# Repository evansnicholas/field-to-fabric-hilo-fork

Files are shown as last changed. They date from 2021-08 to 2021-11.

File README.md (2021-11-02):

# Who is Studio HILO?

Studio HILO is a Berlin-based studio for textile innovation. We rethink the textile industry by offering open tools, trainings and consultancy for small-scale textile manufacturing environments. HILO’s mission is to create playgrounds for independent yarn production. The HILO Spinning Machine (and Software) is an open source project by Studio HILO and allows users to produce their own customized yarn. More information: www.studiohilo.com

# What can you do with the HILO Spinning Machine/Software?

With hardware (HILO Spinning Machine) and software (HILO App) you can create different kinds of yarns. The software helps you to design and plan the yarn digitally – for weaving or knitting textiles. The hardware allows you to spin and twist the personalized yarn, all you have to do is to insert raw fibres of your choice (e.g. wool, silk, plastics) and press play. This is a tool for prototyping and experimenting!

# How does this instruction work?

We made a step by step instruction for materials order, hardware construction and software control. Just follow the order of the folders and in each folder you will find a readme.pdf that instructs you – please read it first of all.

# What are the steps?
* Introduction
* List of Parts
* Files
* Software
* Hardware
* How to start spinning

# What is the status quo of this project?

We documented every part for the HILO Spinning Machine 3.0 / Software but we continue working on both. This project is at an early stage of development, every piece of hardware and software is in beta version.

# How to reach out for support?

We built this, but we need your help to adjust and improve the current prototype. Send us your ideas, experiments, bugs and improvements. We are happy to see our project grow! Get in touch with us via diy@studiohilo.com. Have fun!

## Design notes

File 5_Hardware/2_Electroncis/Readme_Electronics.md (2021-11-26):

# Electronics 

In this scene you will connect all necessary components to make the HILO Spinning Machine work. In the electronic schematic and machine diagram you can see where and how the components are connected.

## Electronic Schematic

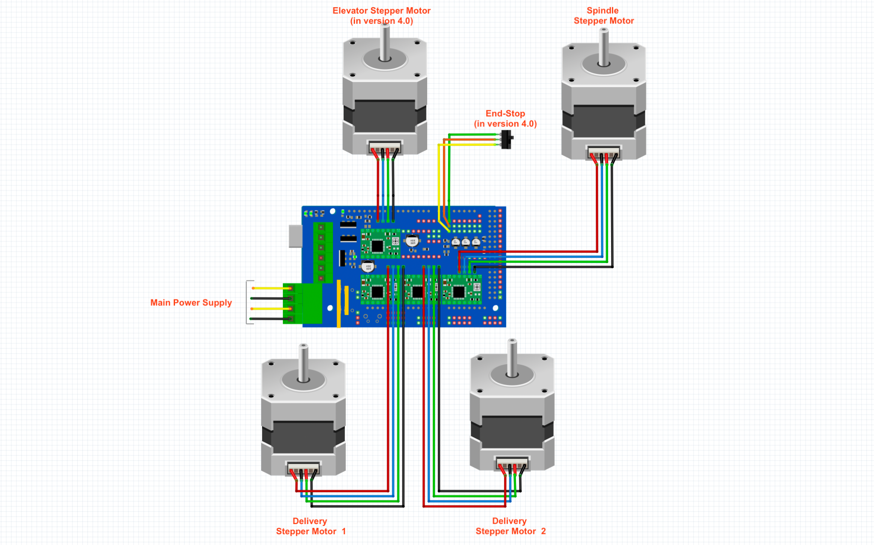
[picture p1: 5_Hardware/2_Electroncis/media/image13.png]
Schematics
  

## Connection Diagram

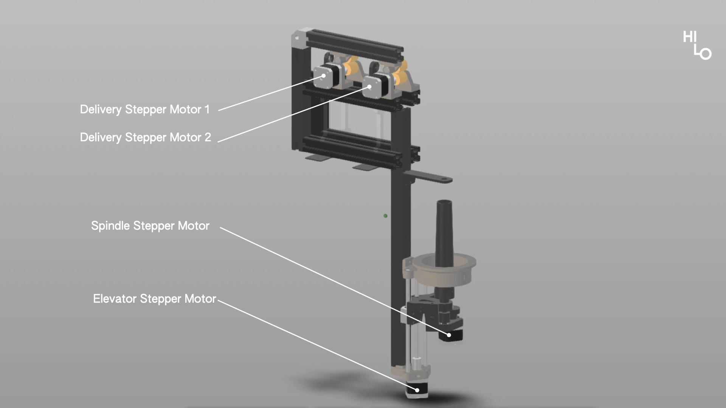
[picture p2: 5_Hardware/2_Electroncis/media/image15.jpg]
assembly
  

    1. Microcontroller Arduino Mega 2560 & RAMPS 1.4

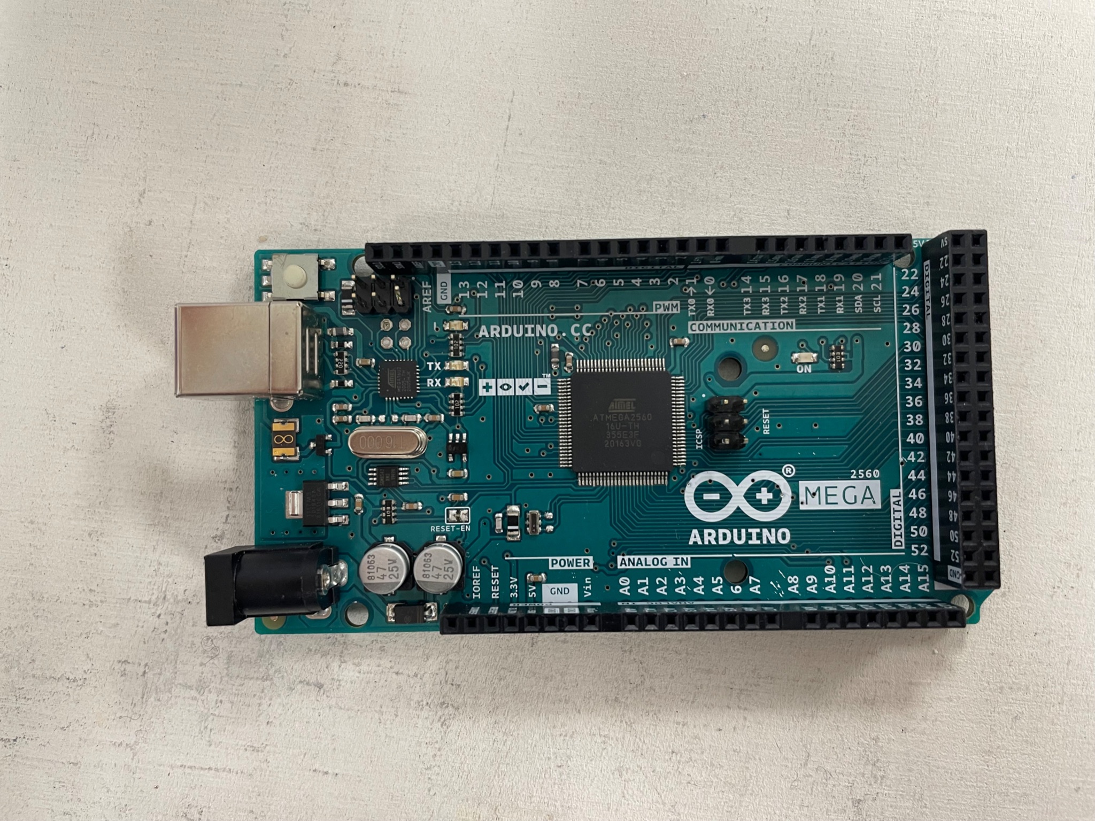
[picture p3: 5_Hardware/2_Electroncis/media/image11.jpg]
arduino
  
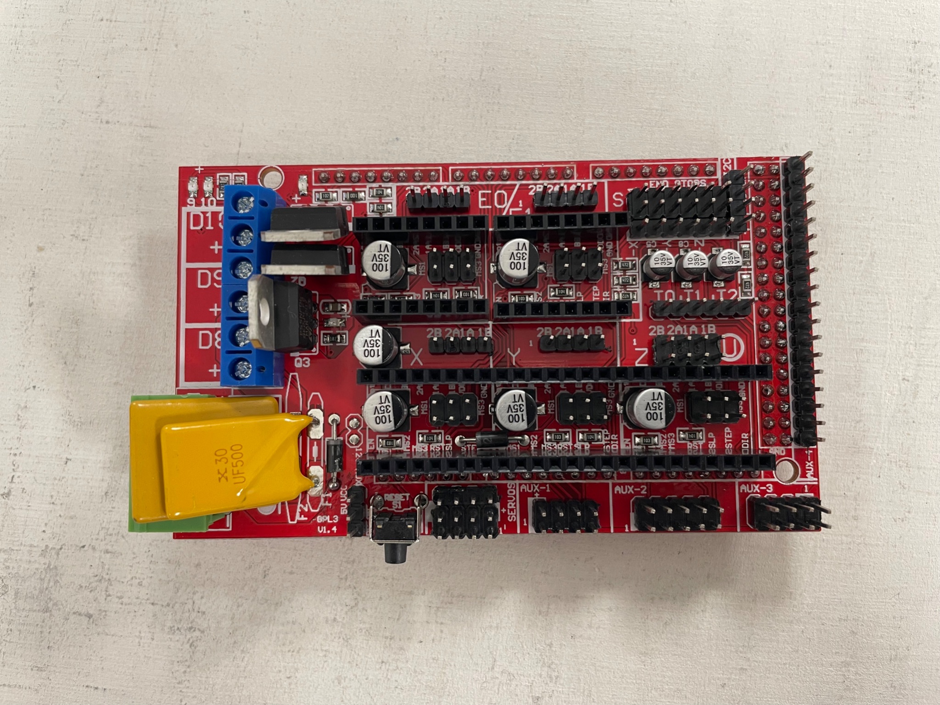
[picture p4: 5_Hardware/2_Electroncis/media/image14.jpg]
ramps1.4
  

    2. Connect the RAMPS board to the Arduino board

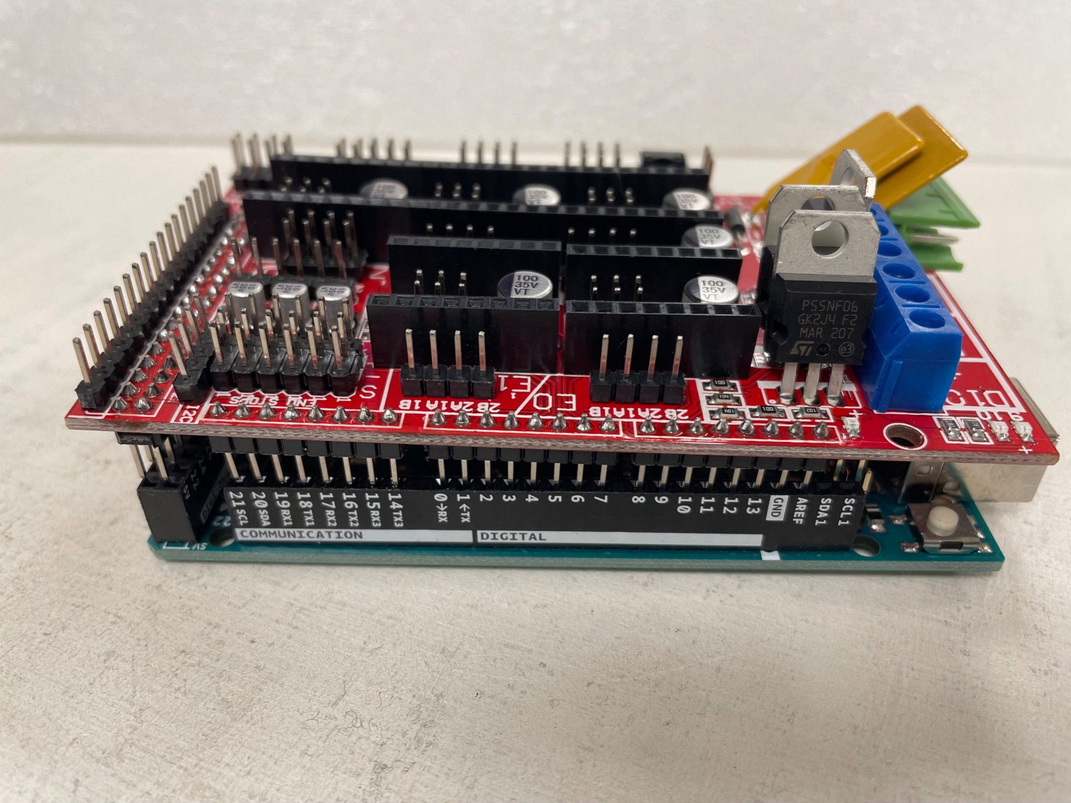
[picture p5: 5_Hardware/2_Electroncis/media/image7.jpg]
connected_boards
  

    3. Glue the Heat Sink to each Driver Modules
 
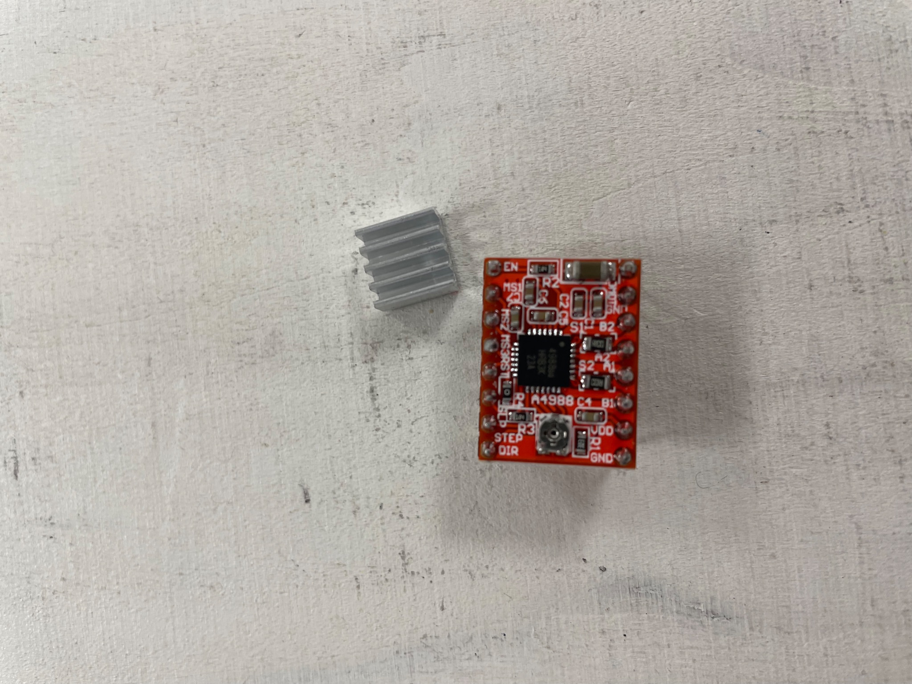
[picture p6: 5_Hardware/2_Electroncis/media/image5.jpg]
heat sink next to driver module
  
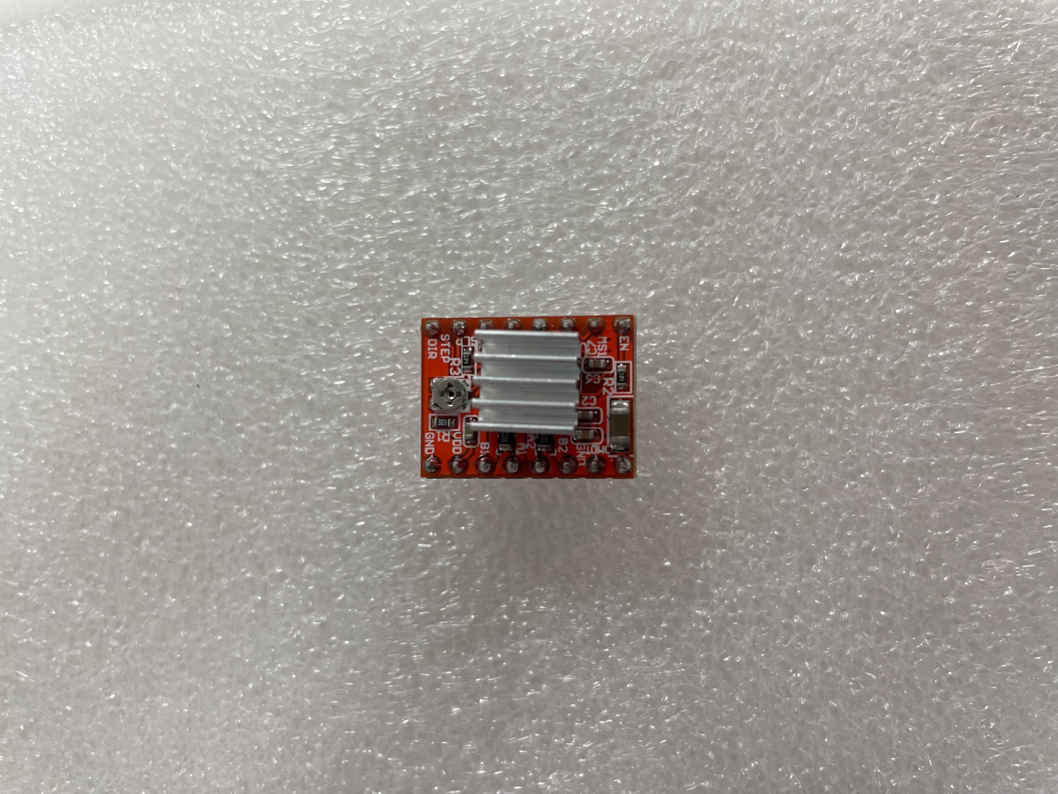
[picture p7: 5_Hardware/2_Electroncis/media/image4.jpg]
heat sink attached
  

    4. Connect the cables to the Stepper Motors 

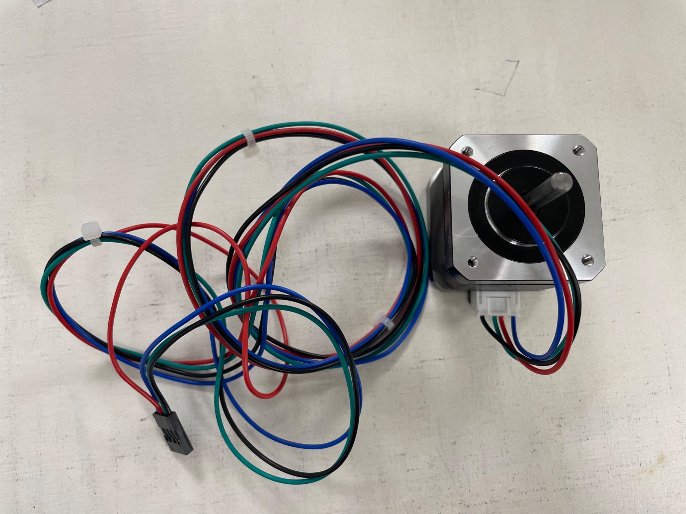
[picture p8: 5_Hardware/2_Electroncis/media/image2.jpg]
  

    5. Connect the Driver Modules* to the board as you see in the image. 

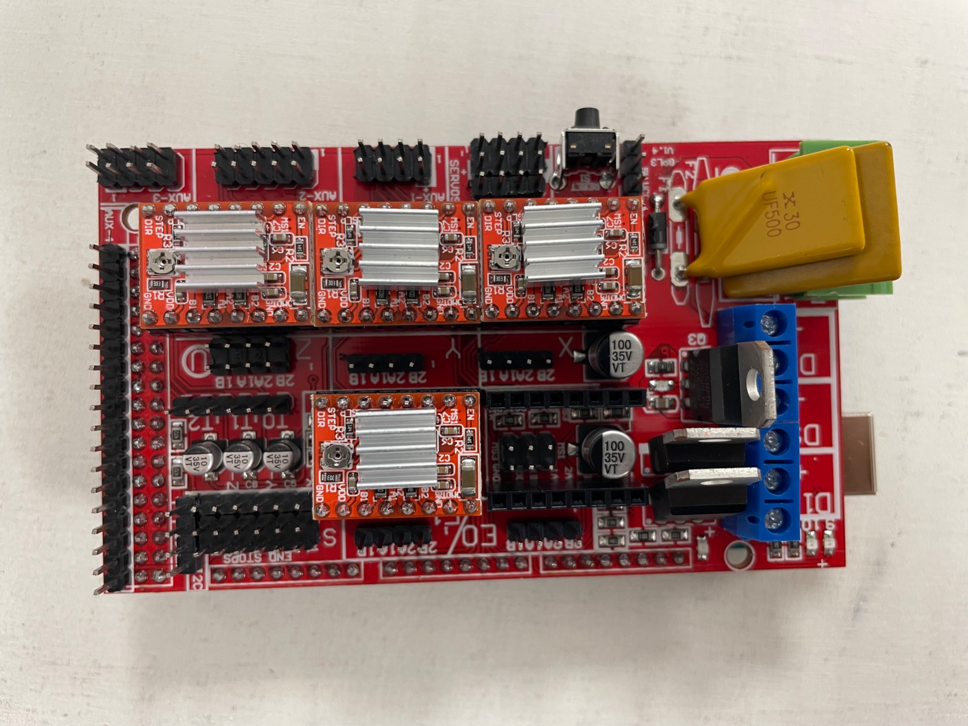
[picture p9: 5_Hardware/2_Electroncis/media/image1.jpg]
  

    6. Connect Delivery Stepper Motor 1 to the Board

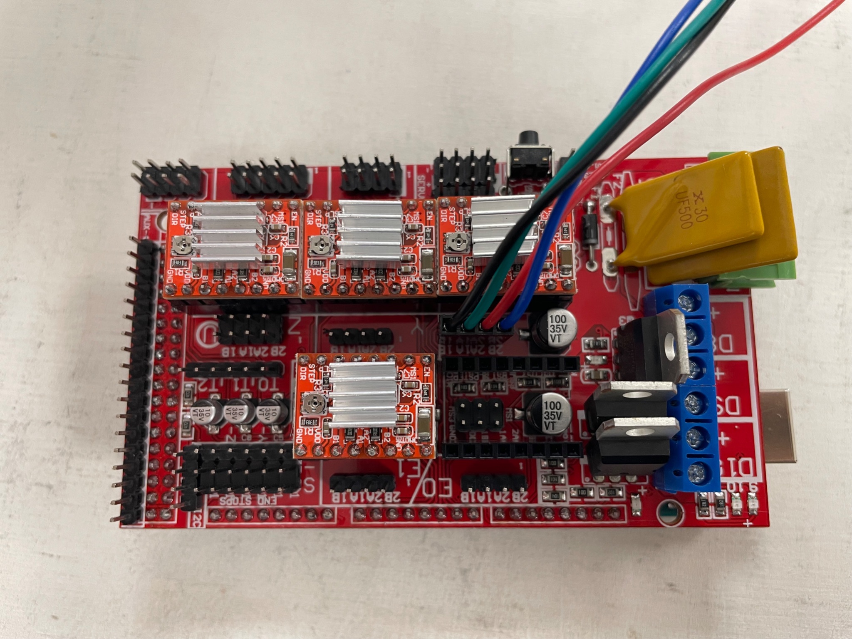
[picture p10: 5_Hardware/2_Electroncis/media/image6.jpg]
stepper motor1
  

    7. Connect Delivery Stepper Motor 2 to the Board

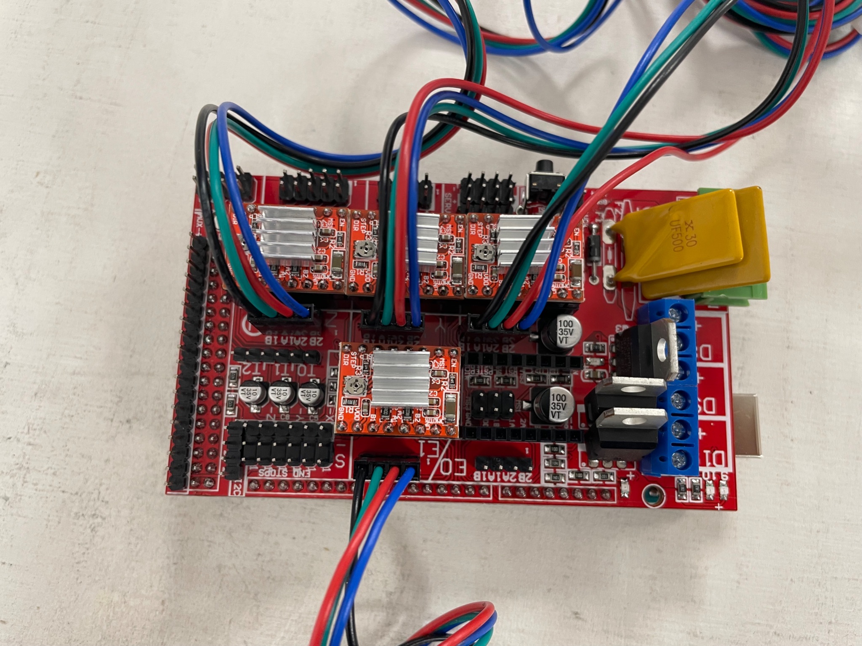
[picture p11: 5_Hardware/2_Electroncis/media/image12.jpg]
stepper motor2
  

    8. Connect Spindle Stepper Motor to the Board

spindle motor  

    9. Connect Elevator Stepper Motor to the Board

elevator motor  

    10. Connection of the power supply to the RAMPS 1.4 Board 

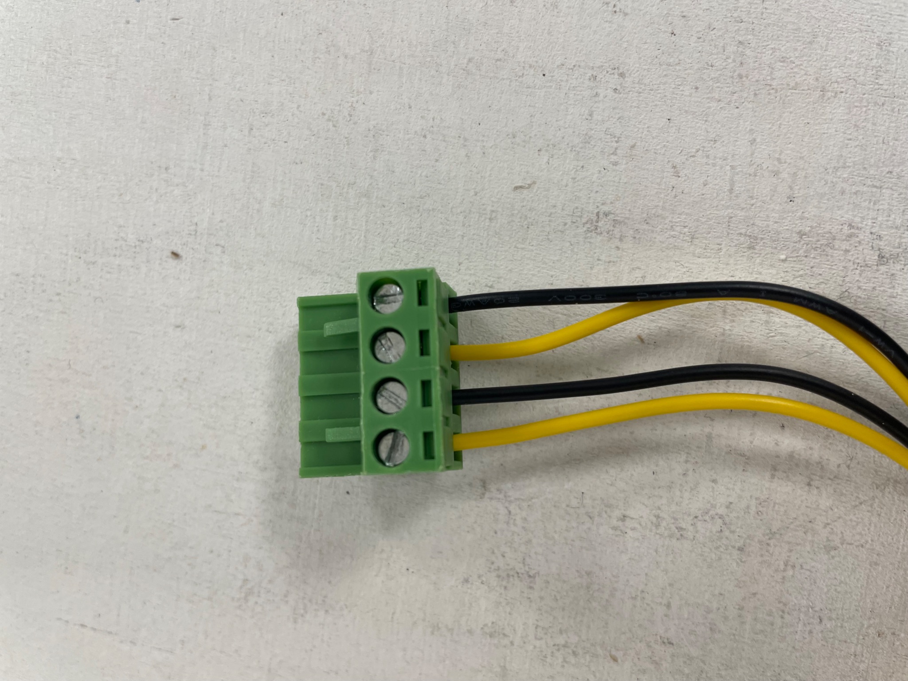
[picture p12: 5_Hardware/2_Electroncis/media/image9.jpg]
adapter
  
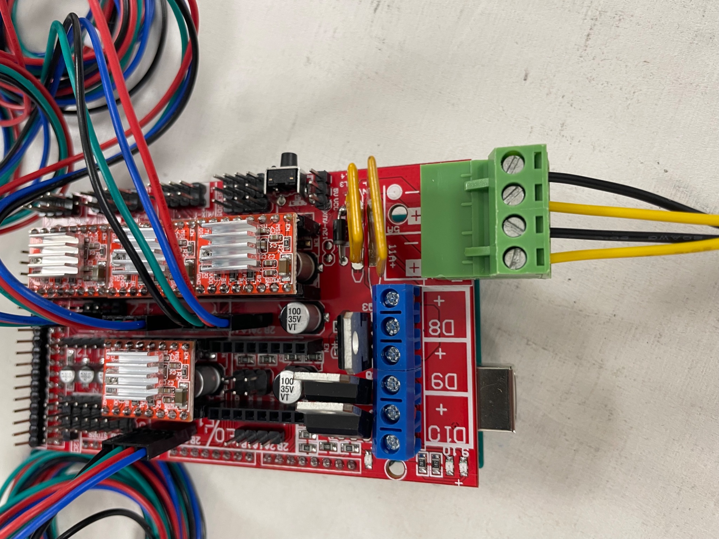
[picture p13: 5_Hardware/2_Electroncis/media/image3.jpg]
connectedtoboard


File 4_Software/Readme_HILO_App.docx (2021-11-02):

HILO App

The HILO app is designed as a user-friendly software to control a HILO spinning machine. The functionality is limited (for now) to controlling the thickness and amount of twist of spun yarn. Users can select a HILO device connected to their computer (via a USB serial port) or use a simulator. The app is written in Processing and can be launched from the Processing IDE, or exported as a stand-alone app for MacOS, Windows or Linux.

Keyboard Controls

The app is made to be used with the mouse or touchpad. A few keyboard shortcuts were left in, which can be helpful when using or debugging.

- c - connect to HILO
- C (uppercase, Shift + c) - disconnect from HILO
- Spacebar - start or stop spinning
- l (lowercase L) - print the list of available serial ports to the console (for debug)
- I (uppercase i, Shift + i) - load a new image (only in pattern mode)

Settings Files

The app is provided with a set of configuration files, within the data/settings/ folder. The files are written in plain text using a JSON format. They can be opened and edited using a simple text editor (e.g. TextEdit, Notepad) and are easy enough to understand and modify. The original names and locations should be kept, as the software is looking for these exact files at the exact location. Descriptions of each file and contents follow.

App Settings

Filename: HILO_AppSettings.json

This file contains basic settings for the app’s behavior and appearance. This includes the size of the viewport window and a reference for the file from which the app’s text is loaded.

- prefPort:thenameofthepreferredserialport,withindoublequotes.Forinstance "COM4" on Windows or "/dev/tty.usbserial001" on Mac OS. You can leave it blank, as just a pair of double quotes "". Whenever you successfully connect to a HILO machine via serial port, the software sets that port as the preferred port and updated the settings file.
- fullscreen:ifsettotrue(noquotes)theappwillstartinfullscreenmodeandignore the width and height settings. If set to false (no quotes) the app’s window size is determined by width and height.
- langFile:thenameofthefile(inquotes)containingtheapp’stext,bydefault "HILO_AppText_EN.json". It would be possible to use a different file, so the app can be translated to other languages.
- widthandheight:positiveintegernumbersdeterminingthesizeoftheapp’swindow, in pixels. If the fullscreen option is set to true then width and height are ignored.

Machine Settings

Filename: HILO_MachineSettings.json

This file contains settings for the HILO machine. Every time a connection is established, these values are set in the machine. The values can’t be changed in the UI. They are pre-determined through tests using the in-house test app.

- deliverySpeedSteps: the speed in steps per second (positive integer value, like300) for the delivery speed. Essentially, the speed at which the machine is running.
- draftingSpeedPercMax:thehighestvalueforthespeedofthedraftingroll,as a percentage of the delivery speed. A positive integer between 0 and 100, like 70. This corresponds to the drafting speed for thick yarn.
- draftingSpeedPercMin:thelowestvalueforthespeedofthedraftingroll,asa percentage of the delivery speed. A positive integer between 0 and 100, like 20. This corresponds to the drafting speed for thin yarn.
- spindleSpeedStepsMax:thespeedinstepspersecond(positiveintegervalue,like700) for the spindle, corresponding to the maximum amount of twist in spin mode.
- spindleSpeedStepsMin:thespeedinstepspersecond(positiveintegervalue,like200) for the spindle, corresponding to the minimum amount of twist in spin mode.

HILO Devices

A HILO device is represented as an abstract in the app, as a HILOInterface (found in the tab HILO_BaseClasses). This defines a common set of operations for any HILO device, and allows us to use an actual device (communicating through a serial port); or a “simulator” so that we can test and demonstrate the app without needing a machine or other hardware. In the future we may wish to define other devices such as remote/networked HILO machines and clusters, or different versions of the HILO machine.

The simulator acts for most (but not all) purposes like an actual machine. As mentioned above, it is meant to replace an actual machine during app testing and quick demos. The simulator class HILOSimulator is defined in the tab HILO_Simulator, whereas the actual HILO (which connects to a serial port and communicates with a machine using the HILO protocol) is implemented as class HILODevice in the tab HILO_Device.

A device or simulator should be assigned a callback handler (implementing the HILOCallbackHandler interface, see the HILO_BaseClasses tab) which gets notified of changes in the state of HILO and acts accordingly. The actual handler used by the app for HILO events is an AppHILOCallbackHandler (implementing the HILOCallbackHandler interface) and can be found in the tab App_Callbacks_HILO.

User Interface

The layout of the UI is based on a mixture of fixed values and reactive behaviour - that is, the position and size of some elements is calculated depending on the size of the app’s window.

Some of the UI elements are based on visual assets (e.g. icons) which can be found in the folder data/icons/ folder. There are different asset folders (small, medium and large) corresponding to different window sizes. The fonts used by the app can be found within the data/fonts/ folder. Fonts are in a vector-format which (contrary to the icons) can be scaled for different sizes without a loss in quality.

The variables, objects and UI setup functions can be found in the UI_All_Layout tab; with special attention to the uiSetup() function, where UI elements are created and laid-out.
The app’s UI is built from a series of UI elements. These are objects descending from class UIBasicElement or otherwise conforming to the UIElement interface (see the tab UI_BaseClasses). Each UI element can be assigned a callback handler (UICallbackHandler object or a descendant, see the same tab) which gets notified of changes in the element and acts accordingly. For instance: when a slider knob is moved, the slider element notifies its handler via the callbackUISliderDragged() callback, and the handler object changes the appearance of another UI element, or triggers an update on the HILO machine.

Classes defining UI elements can be found in tabs with the prefix UI_ and a tab may contain more than one class - for instance UI_BaseClasses or UI_Text. The actual handler used by the app for UI events is an AppUICallbackHandler (extending the original UICallbackHandler) and can be found in the tab App_Callbacks_UI.

Serial Communication Protocol

The HILO machine’s “brain” is an Arduino-based board. The original prototype used an Arduino Uno model with a custom-made shield, whereas the new prototype uses an Arduino Mega 2560 with a RAMPS v1.4 shield. The machine can be controlled by sending simple text-based messages to it via the Arduino’s serial port (USB) running at a speed of 115200 Baud. This is commonly done by an app running a graphic user interface (HILO App) with buttons and sliders, but you can also control the machine “directly” by opening a serial port terminal/monitor (such as the Serial Monitor tool in the Arduino IDE) and typing in the messages yourself between square brackets (https://www.youtube.com/watch?v=pxh87KO5VPU)

The protocol defining the messages and behavior is rather simple. The user or app sends a command to the machine; and the machine replies with a conformation or error. For instance, the app sends a command to start spinning with the drafting speed at 40% of the delivery speed, and the machine confirms that it started spinning:

● app sends message [R,40] which means “run at 40% drafting speed”

● machine replies with [R] which means “I’m running”

Each message (command or reply) is contained in square brackets and consists of an upper-case character and one or two optional parameters (integer numbers).
Once a command is sent, the machine will typically reply with the same command (upper-case character), without parameters, as above. If an error occurs, it replies with an error message, which contains an error code number - for instance [E,6] when receiving an unknown command. Please refer to the firmware for each code’s description.
A machine programmed with a debug-enabled firmware will also send debug messages starting with the character X such as [X,handleCommandRun(): HILO is already spinning]. These are just meant to provide feedback when testing, and are otherwise inconsequential. The HILO app (or rather, the HILODevice class used in the app) prints these messages to the console.

>> Please check our video How to use arduino serial port

https://vimeo.com/639190238

Command | Meaning and reply | Example (command/reply)
[R,n] | Run the machine, with a drafting speed as a percentage of the delivery speed, as an integer number between 0 and 100. Can also be called while the machine is running, to change the drafting speed. Reply: [P] in case of success, or [E,n] in case of error (number or value of parameters, or the elevator is resetting) | [R,70] [R]
[S] | Stop the machine. This can be used while the machine is spinning or resetting the elevator. Reply: [S]. | [S] [S]
[D,n] | Set the speed of the delivery motor(s) in steps/second. Reply: [D] in case of success, or [E,n] in case of error (number of parameters or value). | [D,300] [D]
[P,n] | Set the speed of the spindle motors in steps/second. Reply: [P] in case of success, or [E,n] in case of error | [P,550] [P]
[A] | Ping the machine, which can be used to check if the a HILO machine is connected to a serial port and responding properly. Reply: [A]. | [A] [A]
[T] | Request the machine’s current state. [T] Reply: either [S], [R] or [V] when stopped, running or resetting. | [S] [R] [V]
[I] | Request information about the machine. Mostly useful for debug purposes, or to check which version of the firmware is running in a machine. Reply: a debug message like [X,HILO Firmware 0.1.0. State S. Delivery speed -240. Spindle speed 700. Elevator height 0]

Firmware

The firmware for the HILO machine - that is, the software which runs on the machine itself - is developed using the Arduino IDE and meant to be used in Arduino-compatible boards. The firmware uses the AccelStepper library by Mike McCauley, which can be installed via the Library Manager tool in the Arduino IDE.

>> Check the video How To install HILO Firmware in Arduino

Readme_HILO App_14, July 2021

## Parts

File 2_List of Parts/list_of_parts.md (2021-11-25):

|Type |Component |Amount|Description|Link|
|:---|:---|:---|:---|:---|
|Frame |Makerbeam 3030 T-Slot Nut 8mm Profil |1|540mm|[Aluprofile24](https://aluprofile24.de/product_info.php?info=p209_strebenprofil-30x30mm-nut-8-schwarz---zuschnitt.html)|
|Frame |Makerbeam 3030 T-Slot Nut 8mm Profil |4|230mm|[Aluprofile24](https://aluprofile24.de/product_info.php?info=p209_strebenprofil-30x30mm-nut-8-schwarz---zuschnitt.html)|
|Frame |Makerbeam 3030 T-Slot Nut 8mm Profil |1|210mm|[Aluprofile24](https://aluprofile24.de/product_info.php?info=p209_strebenprofil-30x30mm-nut-8-schwarz---zuschnitt.html)|
|Frame |Makerbeam 3030 T-Slot Nut 8mm Profil |1|135mm|[Aluprofile24](https://aluprofile24.de/product_info.php?info=p209_strebenprofil-30x30mm-nut-8-schwarz---zuschnitt.html)|
|Frame |Makerbeam 3030 T-Slot Nut 8mm Profil |2|200 mm|[Aluprofile24](https://aluprofile24.de/product_info.php?info=p209_strebenprofil-30x30mm-nut-8-schwarz---zuschnitt.html)|
|Frame |Makerbeam 3030 T-Slot Nut 8mm Profil |1|225mm |[Aluprofile24](https://aluprofile24.de/product_info.php?info=p209_strebenprofil-30x30mm-nut-8-schwarz---zuschnitt.html)|
|Hardware|Cylindrical screw M3x10|1|ISO 4762 M3 x 10|Hardware store|
|Hardware|Cylindrical Screw M3x12|4|ISO 4762 M3 x 12|Hardware store|
|Hardware|Cylindrical screw  M3x14|16|ISO 4762 M3 x 14|Hardware store|
|Hardware|Cylindrical screw M3x20|4|ISO 4762 M3 x 20|Hardware store|
|Hardware|Cylindrical screw M3x30|20|ISO 4762 M3 x 30|Hardware store|
|Hardware|Cylindrical screw M4x8|2|ISO 4762 M4 x 14|Hardware store|
|Hardware|Cylindrical screw M4x10|30|ISO 4762 M4 x 9|Hardware store|
|Hardware|Cylindrical screw  M4x14|8|ISO 4762 M4 x 14|Hardware store|
|Hardware|Cylindrical screw  M6x10|30|EN ISO 4762 M6 x 9|Hardware store|
|Hardware|Cylindrical screw  M8x20|4|EN ISO 4762 M8 x 19|Hardware store|
|Hardware|Hexagon Head Screws with Shaft M8 x 80|2|DIN 931 8.8 M8 x 80|Hardware store|
|Hardware|Nut M3|20|ISO 4032 - M3|Hardware store|
|Hardware|Lock Nut M8|2|ISO 4032 - M8|Hardware store|
|Hardware|T-Nut M4|41|GN 505 M4|[tme](https://www.tme.eu/at/details/gn505-10-m4-mb/profil-zubehor/elesa-ganter/gn-505-10-m4-mb/)|
|Hardware|Trapezoidal Screw Nut T8|1||[Amazon](https://www.amazon.com/ReliaBot-300mm-Thread-Starts-Printer/dp/B07B63CVSJ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(Acme%2Bthread%2C%2B2%2Bmm%2Bthread%2Bpitch%2C%2B4%2Bstart%2C%2B8%2Bmm%2Bpitch%29%2Bfor%2B3D%2Bprinters%2Band%2BCNC%2Bmachine%2BZ-axis&qid=1635337457&sr=8-1&th=1)|
|Hardware|Covers|5|30 x 30 cm|[Aluprofile24](https://aluprofile24.de/product_info.php?info=p274_profilabdeckkappe-30x30i.html)|
|Hardware|Hinge for 3030 Profil|1|30 x 30 M8|[Aluprofile24](https://aluprofile24.de/product_info.php?info=p99_gelenk.html)|
|Hardware|Angle with Nut M8 for 3030 Profil|15|30 x 30 M7|Hardware store|
|Hardware|Aluminium Spacer Sleeve|6|EN ISO 845|[Igus](https://www.igus.de/product/60?artNr=GV0SM-0608-06)|
|Hardware|Round Metal Bar|2|D: 8 mm; L: 255 mm|[Azurefilm](https://www.azurefilm.com/en/guides-8mm)|
|Hardware|Round Metal Bar|2|D: 8 mm L: 60 mm|[Azurefilm](https://www.azurefilm.com/en/guides-8mm)|
|Hardware|Round Metal Bar|1|D: 8 mm L: 90 mm|[Azurefilm](https://www.azurefilm.com/en/guides-8mm)|
|Hardware|Bearings|9|8x16x5 mm|[Azurefilm](https://www.azurefilm.com/en/bearing.2)|
|Hardware|Linear bearing|2|SC8UU for 8mm|[Amazon](https://www.amazon.de/-/en/Length-SC8UU-Linear-Bearing-Bushing/dp/B077KQR45N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)|
|Hardware|Motor coupling; D: 5 mm to 8 mm|2|d: 5 mm D: 8 mm|[Aliexpress](https://de.aliexpress.com/item/32961961033.html)|
|Hardware|Elastic Motor Coupling|1|5mm; 8mm|[Amazon](https://www.amazon.com/Fielect-Coupling-Flexible-Connector-Aluminum/dp/B08H5L9TD4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)|
|Hardware|Spindle|1|T8; L: 200 mm|[Amazon](https://www.amazon.com/ReliaBot-300mm-Thread-Starts-Printer/dp/B07B63CVSJ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(Acme%2Bthread%2C%2B2%2Bmm%2Bthread%2Bpitch%2C%2B4%2Bstart%2C%2B8%2Bmm%2Bpitch%29%2Bfor%2B3D%2Bprinters%2Band%2BCNC%2Bmachine%2BZ-axis&qid=1635337457&sr=8-1&th=1)|
|Hardware|GT2 Pulley 20 teeth|1|20 teeth GT2 timing pulley 8mm|[Azurefilm](https://www.azurefilm.com/en/20-or-16-teeth-gt2-timing-pulley)|
|Hardware|GT2 Pulley 40 teeth|1|40 teeth GT2 timing pulley 5mm|[Azurefilm](https://www.azurefilm.com/en/gt2-timing-pulley-8mm-40-teeth)|
|Hardware|Closed Belt Pulley |1|6 mm wide Length: 150m|[Amazon](https://www.amazon.de/gp/product/B075744P4Z/ref=ppx_yo_dt_b_asin_title_o03_s00?ie=UTF8&psc=1)|
|Electronics|Nema 17 Stepper Motor|4|Size: 42x42x39mm 1.5 A 12 V 39 mm 4-Wire 1.8 Deg Stepper Motor with 1 M Wire|[Link](https://www.azurefilm.com/en/ma-17-stepper-motor.2)|
|Electronics|Driver modules|4|Pololu based on A4988|[Pololu](https://www.pololu.com/product/1182)|
|Electronics|Motorshield - RAMPS 1.4 shield|1|Motorshield for aduino Mega|[Mechatronics-pro](https://www.mechatronics-pro.de/de/www.mechatronics-pro.de/de/ramps-1-4-shield-fuer-arduino-mega-mendel-prusa-reprap-1-4a-3d-drucker_631.html)|
|Electronics|Arduino Mega|1|computersystem for running spinningwheel|[Arduino](https://store.arduino.cc/collections/core-family/products/arduino-mega-2560-rev3)|
|Electronics|PC power supply (ATX) + cable|1|420W Akyga AK-B1-420|[Akyga](https://www.akyga.com/products/3-power-supply-atx-ak-b1-420-420w.html)|
|Electronics|Heat sinks|5|Heat Sink 8.8mm x 8.8mm x 5mm|[Amazon](https://www.amazon.com/Silver-Tone-Aluminum-Radiator-8-8mm/dp/B00REFBMZ6)|
|Electronics|Heat-shrink Tubing|1|Holding in place wire|[Amazon](https://www.amazon.com/625pcs-Shrink-Tubing-Tubes-Ratio/dp/B07QM8249H)|
|Electronics|USB Cable||USB Type A Male to Type B Male Printer Scanner Cable|[Amazon](https://www.amazon.com/-/es/impresora-trenzado-velocidad-compatible-Brother/dp/B08Y5NC7GS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)|
|Textile|Velcro Fastener Loop|70 mm|1|[Amazon](https://www.amazon.com/AugTouf-pulgada-adhesivo-resistente-organizaci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)|
|Textile|Velcro Fastener Hook|70 mm|1|[Amazon](https://www.amazon.com/AugTouf-pulgada-adhesivo-resistente-organizaci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)|
|Textile|Poliester Band|200 mm x 20 mm|1|[Amazon](https://www.amazon.de/-/en/kurzwaren-webbing-strap-polypropylene-Widths/dp/B083589CJM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)|
|Printed Parts|Drive Wheel |2|Polyjet Print|More specifications in document 1_Readme_ 3-D printing and laser cutting|
|Printed Parts|Trailing Wheel|2|Polyjet Print|More specifications in document 1_Readme_ 3-D printing and laser cutting|
|Printed Parts|Motor mount|2|PLA Filament 175 |More specifications in document 1_Readme_ 3-D printing and laser cutting|
|Printed Parts|Motor Axle Mount|2|PLA Filament 175|More specifications in document 1_Readme_ 3-D printing and laser cutting|
|Printed Parts|Table lower part|1|PLA Filament 175|More specifications in document 1_Readme_ 3-D printing and laser cutting|
|Printed Parts|Table upper part|1|PLA Filament 175|More specifications in document 1_Readme_ 3-D printing and laser cutting|
|Printed Parts|Spindle|1|PLA Filament 175|More specifications in document 1_Readme_ 3-D printing and laser cutting|
|Printed Parts|Spindle Carrier|1|PLA Filament 175|More specifications in document 1_Readme_ 3-D printing and laser cutting|
|Printed Parts|Printed Axle Holder Trailing Wheel|2|PLA Filament 175|More specifications in document 1_Readme_ 3-D printing and laser cutting|
|Printed Parts|Spinning Ring|1|PLA Filament 175|More specifications in document 1_Readme_ 3-D printing and laser cutting|
|Printed Parts|Elevator Lower Part|1|PLA Filament 175|More specifications in document 1_Readme_ 3-D printing and laser cutting|
|Printed Parts|Yarn Guide Back|1|PLA Filament 175|More specifications in document 1_Readme_ 3-D printing and laser cutting|
|Printed Parts|Yarn Guide Front|1|PLA Filament 175|More specifications in document 1_Readme_ 3-D printing and laser cutting|
|Printed Parts|Hinge Stop|2|PLA Filament 175|More specifications in document 1_Readme_ 3-D printing and laser cutting|
|Printed Parts|Yarn Outlet|1|PLA Filament 175|More specifications in document 1_Readme_ 3-D printing and laser cutting|
|Tools|Level|1||Hardware store|
|Tools|Screw clamps|2||Hardware store|
|Tools|Measuring Tape|1||Hardware store|
|Tools|Caliper|1||Hardware store|
|Tools|Contact glue|1||Hardware store|
|Tools|Instant glue|1||Hardware store|
|Tools|Tap wrench |1 |DIN 352 M8|Hardware store [Youtube](https://www.youtube.com/watch?v=S_FIGFhsWW4)|
|Tools|Metal saw|1|For metal|Hardware store|
|Tools|Allen key set|1|For M3 to M8 |Hardware store|

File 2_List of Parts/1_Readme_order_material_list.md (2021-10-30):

# How to work with this material list?

Please carefully read this introduction before ordering.
We tried to make the order process as easy as possible: All product names are in the order
list – we recommend to tick them off the check list once ordered.
This material list is only a suggestion and based on orders from Germany. Feel free to
choose other materials but be aware about the parts that only work from the same brand
(see descriptions).
We tried to make it understandable for everybody, not only for advanced builders. So if you
never built machines before in your life, you can do it! This HILO Spinning Machine/Software
is a third prototype and it works great but you have to reassemble it yourself.
Don’t hesitate to get in touch if you need support, have notes or feedback:
diy@studiohilo.com

# What to be aware of...

... with extrusions (profiles)?
If you order the aluminium extrusions (profiles) for your machine be aware to order each part
by the same company, same size, same profiles. Otherwise later on things will not fit well;
especially be aware of the T-Nuts.

# ... with electronics?

All electronics have a number in the description, be aware to order the correct number (also
when ordering in other shops). Also double-check the connections, e.g. if they are the same
from the wires to the stepper motor. If you should have doubts, ask us.
When ordering the Arduino mega, please order the original one. We know that it’s a bit more
expensive but it will save you frustration and time – and you support their cool open source
business.

# ... with screws, bolts und nuts?

We tried to have the same size of screws, bolt and nuts. We use M8, M2, M4 and M3
screws, with crosshead or hex.. You can find the screws, bolts and nuts in every length you
need in hardware stores all around (Germany).
Angels and mounting already include the needed screws (if you order it from the link in the
material list), so you don’t need to buy them additionally.

# ... when ordering in general?

Sometimes it takes you three times to order the right part, we’ve been there. Always keep
the receipt and make sure you have a retour voucher. The order process takes about 3
weeks. Order first and use the delivery time to print and produce the 3-D and laser cutting
parts (next folder). Ordering process can be exhausting but don’t give up, because the fun
part is about to start!

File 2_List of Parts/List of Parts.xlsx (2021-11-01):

Type | Component | Amount | Description | Link
Frame | Makerbeam 3030 T-Slot Nut 8mm Profil | 1 | 540mm | https://aluprofile24.de/product_info.php
Frame | Makerbeam 3030 T-Slot Nut 8mm Profil | 4 | 230mm | https://aluprofile24.de/product_info.php
Frame | Makerbeam 3030 T-Slot Nut 8mm Profil | 1 | 210mm | https://aluprofile24.de/product_info.php
Frame | Makerbeam 3030 T-Slot Nut 8mm Profil | 1 | 135mm | https://aluprofile24.de/product_info.php
Frame | Makerbeam 3030 T-Slot Nut 8mm Profil | 2 | 200 mm | https://aluprofile24.de/product_info.php
Frame | Makerbeam 3030 T-Slot Nut 8mm Profil | 1 | 225mm | https://aluprofile24.de/product_info.php
Hardware | Cylindrical screw M3x10 | 1 | ISO 4762 M3 x 10 | Hardware store
Hardware | Cylindrical Screw M3x12 | 4 | ISO 4762 M3 x 12 | Hardware store
Hardware | Cylindrical screw M3x14 | 16 | ISO 4762 M3 x 14 | Hardware store
Hardware | Cylindrical screw M3x20 | 4 | ISO 4762 M3 x 20 | Hardware store
Hardware | Cylindrical screw M3x30 | 20 | ISO 4762 M3 x 30 | Hardware store
Hardware | Cylindrical screw M4x8 | 2 | ISO 4762 M4 x 14 | Hardware store
Hardware | Cylindrical screw M4x10 | 30 | ISO 4762 M4 x 9 | Hardware store
Hardware | Cylindrical screw M4x14 | 8 | ISO 4762 M4 x 14 | Hardware store
Hardware | Cylindrical screw M6x10 | 30 | EN ISO 4762 M6 x 9 | Hardware store
Hardware | Cylindrical screw M8x20 | 4 | EN ISO 4762 M8 x 19 | Hardware store
Hardware | Hexagon Head Screws with Shaft M8 x 80 | 2 | DIN 931 8.8 M8 x 80 | Hardware store
Hardware | Nut M3 | 20 | ISO 4032 - M3 | Hardware store
Hardware | Lock Nut M8 | 2 | ISO 4032 - M8 | Hardware store
Hardware | T-Nut M4 | 41 | GN505 M4 | https://www.tme.eu/at/details/gn505-10-m4-mb/profil-zubehor/elesa-ganter/gn-505-10-m4-mb/
Hardware | Trapezoidal Screw Nut T8 | 1 |  | https://www.amazon.com/ReliaBot-300mm-Thread-Starts-Printer/dp/B07B63CVSJ
Hardware | Covers | 5 | 30 x 30 cm | https://aluprofile24.de/product_info.php?info=p274_profilabdeckkappe-30x30i.html
Hardware | Hinge for 3030 Profil | 1 | 30 x 30 M8 | https://aluprofile24.de/product_info.php?info=p99_gelenk.html
Hardware | Angle with Nut M8 for 3030 Profil | 15 | 30 x 30 M7 | Hardware store
Hardware | Aluminium Spacer Sleeve | 6 | EN ISO 845 | https://www.igus.de/product/60?artNr=GV0SM-0608-06
Hardware | Round Metal Bar | 2 | D: 8 mm; L: 255 mm | https://www.azurefilm.com/en/guides-8mm
Hardware | Round Metal Bar | 2 | D: 8 mm, L: 60 mm | https://www.azurefilm.com/en/guides-8mm
Hardware | Round Metal Bar | 1 | D: 8 mm, L: 90 mm | https://www.azurefilm.com/en/guides-8mm
Hardware | Bearings | 9 | 8x16x5 mm | https://www.azurefilm.com/en/bearing.2
Hardware | Linear bearing | 2 | SC8UU for 8mm | https://www.amazon.de/-/en/Length-SC8UU-Linear-Bearing-Bushing/dp/B077KQR45N?qsid=259-4068372-5802129
Hardware | Motor coupling; D: 5 mm to 8 mm | 2 | d: 5 mm, D: 8 mm | https://de.aliexpress.com/item/32961961033.html
Hardware | Elastic Motor Coupling | 1 | 5mm; 8mm | https://www.amazon.com/Fielect-Coupling-Flexible-Connector-Aluminum/dp/B08H5L9TD4
Hardware | Spindle | 1 | T8; L: 200 mm | https://www.amazon.com/ReliaBot-300mm-Thread-Starts-Printer/dp/B07B63CVSJ
Hardware | GT2 Pulley 20 teeth | 1 | 20 teeth GT2 timing pulley 8mm | https://www.azurefilm.com/en/20-or-16-teeth-gt2-timing-pulley
Hardware | GT2 Pulley 40 teeth | 1 | 40 teeth GT2 timing pulley 5mm | https://www.azurefilm.com/en/gt2-timing-pulley-8mm-40-teeth
Hardware | Closed Belt Pulley | 1 | 6 mm wide Length: 150m | https://www.amazon.de/gp/product/B075744P4Z/ref=ppx_yo_dt_b_asin_title_o03_s00?ie=UTF8&psc=1
Electronics | Nema 17 Stepper Motor | 4 | Size: 42x42x39mm 1.5 A 12 V 39 mm, 4-Wire 1.8 Deg Stepper Motor with 1 M Wire | https://www.azurefilm.com/en/ma-17-stepper-motor.2
Electronics | Driver modules | 4 | Pololu, based on A4988 | https://www.pololu.com/product/1182
Electronics | Motorshield - RAMPS 1.4 shield | 1 | Motorshield for aduino Mega | https://www.mechatronics-pro.de/de/www.mechatronics-pro.de/de/ramps-1-4-shield-fuer-arduino-mega-mendel-prusa-reprap-1-4a-3d-drucker_631.html
Electronics | Arduino Mega | 1 | computersystem for running spinningwheel | https://store.arduino.cc/collections/core-family/products/arduino-mega-2560-rev3
Electronics | PC power supply (ATX) + cable | 1 | 420W, Akyga AK-B1-420 | https://www.akyga.com/products/3-power-supply-atx-ak-b1-420-420w.html
Electronics | Heat sinks | 5 | Heat Sink 8.8mm x 8.8mm x 5mm | https://www.amazon.com/Silver-Tone-Aluminum-Radiator-8-8mm/dp/B00REFBMZ6
Electronics | Heat-shrink Tubing | 1 | Holding in place wire | https://www.amazon.com/625pcs-Shrink-Tubing-Tubes-Ratio/dp/B07QM8249H
Electronics | USB Cable |  | USB Type A Male to Type B Male Printer Scanner Cable | https://www.amazon.com/-/es/impresora-trenzado-velocidad-compatible-Brother/dp/B08Y5NC7GS?__mk_es_US=ÅMÅŽÕÑ
Textile | Velcro Fastener Loop | 70 mm | 1 | https://www.amazon.com/AugTouf-pulgada-adhesivo-resistente-organización/dp/B09BJFYT6X?__mk_es_US=ÅMÅŽÕÑ
Textile | Velcro Fastener Hook | 70 mm | 1 | https://www.amazon.com/AugTouf-pulgada-adhesivo-resistente-organización/dp/B09BJFYT6X?__mk_es_US=ÅMÅŽÕÑ
Textile | Poliester Band | 200 mm x 20 mm | 1 | https://www.amazon.de/-/en/kurzwaren-webbing-strap-polypropylene-Widths/dp/B083589CJM
Printed Parts | Drive Wheel | 2 | Polyjet Print | More specifications in document 1_Readme_ 3-D printing and laser cutting
Printed Parts | Trailing Wheel | 2 | Polyjet Print | More specifications in document 1_Readme_ 3-D printing and laser cutting
Printed Parts | Motor mount | 2 | PLA Filament 1,75 | More specifications in document 1_Readme_ 3-D printing and laser cutting
Printed Parts | Motor Axle Mount | 2 | PLA Filament 1,75 | More specifications in document 1_Readme_ 3-D printing and laser cutting
Printed Parts | Table lower part | 1 | PLA Filament 1,75 | More specifications in document 1_Readme_ 3-D printing and laser cutting
Printed Parts | Table upper part | 1 | PLA Filament 1,75 | More specifications in document 1_Readme_ 3-D printing and laser cutting
Printed Parts | Spindle | 1 | PLA Filament 1,75 | More specifications in document 1_Readme_ 3-D printing and laser cutting
Printed Parts | Spindle Carrier | 1 | PLA Filament 1,75 | More specifications in document 1_Readme_ 3-D printing and laser cutting
Printed Parts | Printed Axle Holder Trailing Wheel | 2 | PLA Filament 1,75 | More specifications in document 1_Readme_ 3-D printing and laser cutting
Printed Parts | Spinning Ring | 1 | PLA Filament 1,75 | More specifications in document 1_Readme_ 3-D printing and laser cutting
Printed Parts | Elevator Lower Part | 1 | PLA Filament 1,75 | More specifications in document 1_Readme_ 3-D printing and laser cutting
Printed Parts | Yarn Guide Back | 1 | PLA Filament 1,75 | More specifications in document 1_Readme_ 3-D printing and laser cutting
Printed Parts | Yarn Guide Front | 1 | PLA Filament 1,75 | More specifications in document 1_Readme_ 3-D printing and laser cutting
Printed Parts | Hinge Stop | 2 | PLA Filament 1,75 | More specifications in document 1_Readme_ 3-D printing and laser cutting
Printed Parts | Yarn Outlet | 1 | PLA Filament 1,75 | More specifications in document 1_Readme_ 3-D printing and laser cutting
Tools | Level | 1 |  | Hardware store
Tools | Screw clamps | 2 |  | Hardware store
Tools | Measuring Tape | 1 |  | Hardware store
Tools | Caliper | 1 |  | Hardware store
Tools | Contact glue | 1 |  | Hardware store
Tools | Instant glue | 1 |  | Hardware store
Tools | Tap wrench M8 | 1 | https://www.youtube.com/watch?v=S_FIGFhsWW4 | Hardware store
Tools | Metal saw | 1 | For metal | Hardware store
Tools | Allen key set | 1 | For M3 to M8 | Hardware store

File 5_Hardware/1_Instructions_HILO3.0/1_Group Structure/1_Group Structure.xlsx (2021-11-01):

 | Description of Groups Components Description
 | Group Structure
Type | Component | Amount | Description | Link
Frame | Makerbeam 3030 T-Slot Nut 8mm Profil | 1 | 540mm | https://aluprofile24.de/product_info.php
Frame | Makerbeam 3030 T-Slot Nut 8mm Profil | 4 | 230mm | https://aluprofile24.de/product_info.php
Frame | Makerbeam 3030 T-Slot Nut 8mm Profil | 1 | 210mm | https://aluprofile24.de/product_info.php
Frame | Makerbeam 3030 T-Slot Nut 8mm Profil | 1 | 135mm | https://aluprofile24.de/product_info.php
Frame | Makerbeam 3030 T-Slot Nut 8mm Profil | 2 | 200 mm | https://aluprofile24.de/product_info.php
Frame | Makerbeam 3030 T-Slot Nut 8mm Profil | 1 | 225mm | https://aluprofile24.de/product_info.php
Hardware | Angle with Nut M8 for 3030 Profil | 15 | 30 x 30 M7 | Hardware store
Hardware | Cylindrical screw M4x10 | 30 | ISO 4762 M4 x 9 | Hardware store
Hardware | Cylindrical screw M8x20 | 2 | EN ISO 4762 M8 x 19 | Hardware store
Hardware | Cylindrical screw M6x10 | 30 | EN ISO 4762 M6 x 9 | Hardware store
Hardware | Covers | 5 | 30 x 29 | https://aluprofile24.de/product_info.php?info=p274_profilabdeckkappe-30x30i.html
Hardware | Hinge for 3030 Profil | 1 | 30 x 30 M7 | https://aluprofile24.de/product_info.php?info=p99_gelenk.html
Hardware | T-Nut M4 | 30 | GN505 M4 | https://www.tme.eu/at/details/gn505-10-m4-mb/profil-zubehor/elesa-ganter/gn-505-10-m4-mb/

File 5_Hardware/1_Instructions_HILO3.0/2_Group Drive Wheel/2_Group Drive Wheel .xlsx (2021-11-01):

 | Description of Groups Components Description
 | Group: Drive Wheel
Type | Component | For Group | Total machine | Description | Links
Hardware | Cylindrical screw M4x14 | 2 | 4 | ISO 4762 M4 x 14 | Hardware store
Hardware | Cylindrical screw M3x14 | 4 | 8 | ISO 4762 M3 x 14 | Hardware store
Hardware | T-Nut M4 | 2 | 4 | GN505 M4 | https://www.tme.eu/at/details/gn505-10-m4-mb/profil-zubehor/elesa-ganter/gn-505-10-m4-mb/
Hardware | Round Metal Bar | 1 | 2 | D: 8 mm, L: 60 mm | https://www.azurefilm.com/en/guides-8mm
Hardware | Bearings | 1 | 2 | 8x16x5 mm | https://www.azurefilm.com/en/bearing.2
Hardware | Motor coupling; D: 5 mm to 8 mm | 1 | 2 | d: 5 mm, D: 8 mm | https://de.aliexpress.com/item/32961961033.html
Printed Parts | Motor mount | 1 | 2 | PLA Filament 1,75 | More specifications in document 1_Readme_ 3-D printing and laser cutting
Printed Parts | Motor Axle Mount | 1 | 2 | PLA Filament 1,75 | More specifications in document 1_Readme_ 3-D printing and laser cutting
Printed Parts | Drive Wheel | 1 | 2 | Polyjet Print | More specifications in document 1_Readme_ 3-D printing and laser cutting
Electronics | Nema 17 Stepper Motor | 1 | 2 | Size: 42x42x39mm 1.5 A 12 V 39 mm, 4-Wire 1.8 Deg Stepper Motor with 1 M Wire | https://www.azurefilm.com/en/ma-17-stepper-motor.2

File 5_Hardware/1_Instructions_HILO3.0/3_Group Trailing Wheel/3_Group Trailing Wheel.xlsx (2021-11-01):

 | Description of Groups Components Description
 | Group: Trailing Wheel
Type | Component | For Group | Total machine | Description | Links
Hardware | Hexagon Head Screws with Shaft M8 x 80 | 1 | 2 | DIN 931 8.8 M8 x 80 | Hardware store
Hardware | T-Nut M4 | 2 | 4 | GN505 M4 | https://www.tme.eu/at/details/gn505-10-m4-mb/profil-zubehor/elesa-ganter/gn-505-10-m4-mb/
Hardware | Cylindrical screw M4x14 | 2 | 4 | ISO 4762 M4 x 14 | Hardware store
Hardware | Lock Nut M8 | 1 | 2 | ISO 4032 - M8 | Hardware store
Hardware | Bearings | 1 | 2 | 8x16x5 mm | https://www.azurefilm.com/en/bearing.2
Hardware | Aluminium Spacer Sleeve | 2 | 4 | EN ISO 846 | https://www.igus.de/product/60?artNr=GV0SM-0608-06
Printed Parts | Trailing Wheel | 1 | 2 | Polyjet Print | More specifications in document 1_Readme_ 3-D printing and laser cutting
Printed Parts | Printed Axle Holder Trailing Wheel | 1 | 2 | PLA Filament 1,75 | More specifications in document 1_Readme_ 3-D printing and laser cutting

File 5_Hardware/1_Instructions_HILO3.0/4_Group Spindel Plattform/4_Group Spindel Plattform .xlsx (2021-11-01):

 | Description of Groups Components Description
 | Group: Spindel Plattform
Type | Component | Amount | Description | Link
Hardware | Cylindrical screw M3x10 | 1 | ISO 4762 M3 x 10 | Hardware store
Hardware | Cylindrical Screw M3x12 | 4 | ISO 4762 M3 x 12 | Hardware store
Hardware | Cylindrical Screw M3x30 | 16 | ISO 4762 M3 x 30 | Hardware store
Hardware | Nut M3 | 16 | ISO 4032 - M3 | Hardware store
Hardware | Spacer Sleeve | 2 | ISO 845 | Hardware store
Hardware | Trapezoidal Screw Nut T8 | 1 |  | https://www.amazon.com/ReliaBot-300mm-Thread-Starts-Printer/dp/B07B63CVSJ
Hardware | Round Metal Bar | 1 | D: 8 mm, L: 90 mm | https://www.azurefilm.com/en/guides-8mm
Hardware | Spindle | 1 | T8; L: 200 mm | https://www.amazon.com/ReliaBot-300mm-Thread-Starts-Printer/dp/B07B63CVSJ
Hardware | Linear bearing | 2 | SC8UU for 8mm | https://www.amazon.de/-/en/Length-SC8UU-Linear-Bearing-Bushing/dp/B077KQR45N?qsid=259-4068372-5802129
Hardware | Bearing | 2 | 8x16x5 mm | https://www.azurefilm.com/en/bearing.2
Hardware | GT2 Pulley 20 teeth | 1 | 20 teeth GT2 timing pulley 8mm | https://www.azurefilm.com/en/20-or-16-teeth-gt2-timing-pulley
Hardware | GT2 Pulley 40 teeth | 1 | 40 teeth GT2 timing pulley 5mm | https://www.azurefilm.com/en/gt2-timing-pulley-8mm-40-teeth
Hardware | Closed Belt Pulley | 1 | 6 mm Length: 150m | https://www.amazon.de/gp/product/B075744P4Z/ref=ppx_yo_dt_b_asin_title_o03_s00?ie=UTF8&psc=1
Printed Parts | Table lower part | 1 | PLA Filament 1,75 | More specifications in document 1_Readme_ 3-D printing and laser cutting
Printed Parts | Table upper part | 1 | PLA Filament 1,75 | More specifications in document 1_Readme_ 3-D printing and laser cutting
Printed Parts | Spindle | 1 | PLA Filament 1,75 | More specifications in document 1_Readme_ 3-D printing and laser cutting
Printed Parts | Spindle Carrier | 1 | PLA Filament 1,75 | More specifications in document 1_Readme_ 3-D printing and laser cutting
Electronics | Nema 17 Stepper Motor | 1 | Size: 42x42x39mm 1.5 A 12 V 39 mm, 4-Wire 1.8 Deg Stepper Motor with 1 M Wire | https://www.azurefilm.com/en/ma-17-stepper-motor.2

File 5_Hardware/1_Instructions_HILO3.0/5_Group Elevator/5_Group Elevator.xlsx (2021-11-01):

 | Description of Groups Components Description
 | Group: Elevator
Type | Component | Amount | Description | Link
Hardware | Cylindrical screw M3x20 | 4 | ISO 4762 M3 x 20 | Hardware store
Hardware | Cylindrical screw M8x20 | 1 | EN ISO 4762 M8 x 19 | Hardware store
Hardware | Cylindrical screw M3x30 | 4 | ISO 4762 M3 x 30 | Hardware store
Hardware | Cylindrical screw M4x14 | 1 | ISO 4762 M4 x 14 | Hardware store
Hardware | Nut M3 | 4 | ISO 4032 - M3 | Hardware store
Hardware | T-Nut M4 | 1 | GN505 M4 | https://www.tme.eu/at/details/gn505-10-m4-mb/profil-zubehor/elesa-ganter/gn-505-10-m4-mb/
Hardware | Round Metal Bar | 2 | D: 8 mm; L: 255 mm | https://www.azurefilm.com/en/guides-8mm
Hardware | Elastic Motor Coupling | 1 | 5mm; 8mm | https://www.amazon.com/Fielect-Coupling-Flexible-Connector-Aluminum/dp/B08H5L9TD4
Hardware | Bearing | 1 | 8x16x5 mm | https://www.azurefilm.com/en/bearing.2
Electronics | Nema 17 Stepper Motor | 1 | Size: 42x42x39mm 1.5 A 12 V 39 mm, 4-Wire 1.8 Deg Stepper Motor with 1 M Wire | https://www.azurefilm.com/en/ma-17-stepper-motor.2
Printed Parts | Spinning Ring | 1 | PLA Filament 1,75 | More specifications in document 1_Readme_ 3-D printing and laser cutting
Printed Parts | Elevator Lower Part | 1 | PLA Filament 1,75 | More specifications in document 1_Readme_ 3-D printing and laser cutting

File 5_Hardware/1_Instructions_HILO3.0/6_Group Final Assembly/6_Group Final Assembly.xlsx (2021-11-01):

 | Description of Groups Components Description
 | Group: Final Assembly
Type | Component | Amount | Description | Link
Hardware | Cylindrical screw M8x20 | 1 | ISO 4762 M8 x 20 | Hardware store
Hardware | Cylindrical screw M4x14 | 1 | ISO 4762 M4 x 14 | Hardware store
Hardware | Cylindrical screw M4x8 | 2 | ISO 4762 M4 x 14 | Hardware store
Hardware | T-Nut M4 | 2 | GN505 M4 | https://www.tme.eu/at/details/gn505-10-m4-mb/profil-zubehor/elesa-ganter/gn-505-10-m4-mb/
Printed Parts | Yarn Guide Back | 1 | PLA Filament 1,75 | More specifications in document 1_Readme_ 3-D printing and laser cutting
Printed Parts | Yarn Guide Front | 1 | PLA Filament 1,75 | More specifications in document 1_Readme_ 3-D printing and laser cutting
Printed Parts | Hinge Stop | 2 | PLA Filament 1,75 | More specifications in document 1_Readme_ 3-D printing and laser cutting
Printed Parts | Yarn Outlet | 1 | PLA Filament 1,75 | More specifications in document 1_Readme_ 3-D printing and laser cutting
Textile | Velcro Fastener Loop | 1 | 70 mm x 15 mm | https://www.amazon.com/AugTouf-pulgada-adhesivo-resistente-organización/dp/B09BJFYT6X?__mk_es_US=ÅMÅŽÕÑ
Textile | Velcro Fastener Hook | 1 | 70 mm x 15 mm | https://www.amazon.com/AugTouf-pulgada-adhesivo-resistente-organización/dp/B09BJFYT6X?__mk_es_US=ÅMÅŽÕÑ
Textile | Poliester Band | 1 | 200 mm x 20 mm | https://www.amazon.de/-/en/kurzwaren-webbing-strap-polypropylene-Widths/dp/B083589CJM

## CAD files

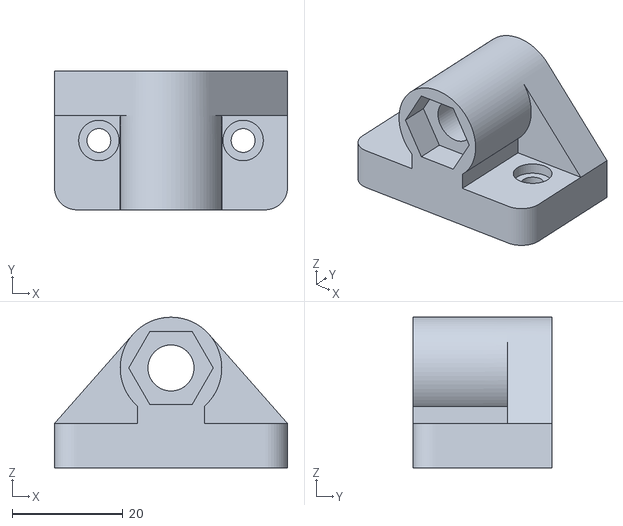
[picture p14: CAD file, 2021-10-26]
3_Files/2_3D CAD/3D CAD Parts/Filament/Axle_holder_trailing_wheel_2.stl
42.0 x 25.0 x 27.1

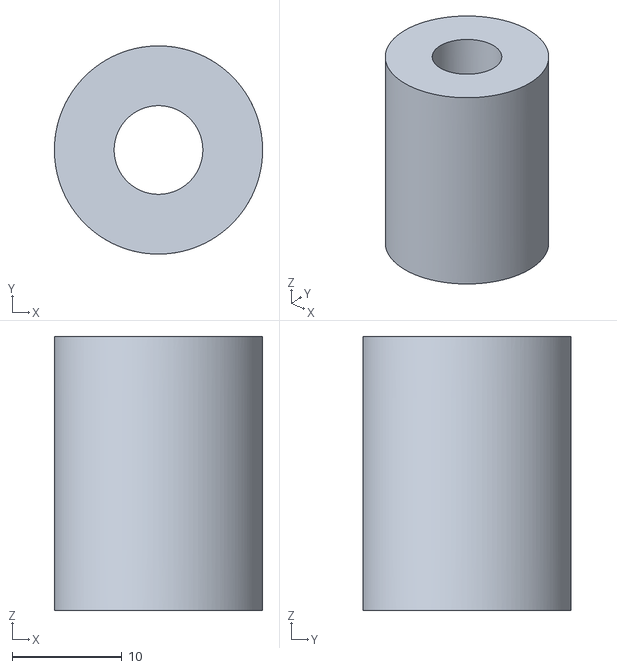
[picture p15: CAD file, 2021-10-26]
3_Files/2_3D CAD/3D CAD Parts/PolyJet/Drive wheel/Drive_wheel_Hard.stl
19.0 x 19.0 x 25.0

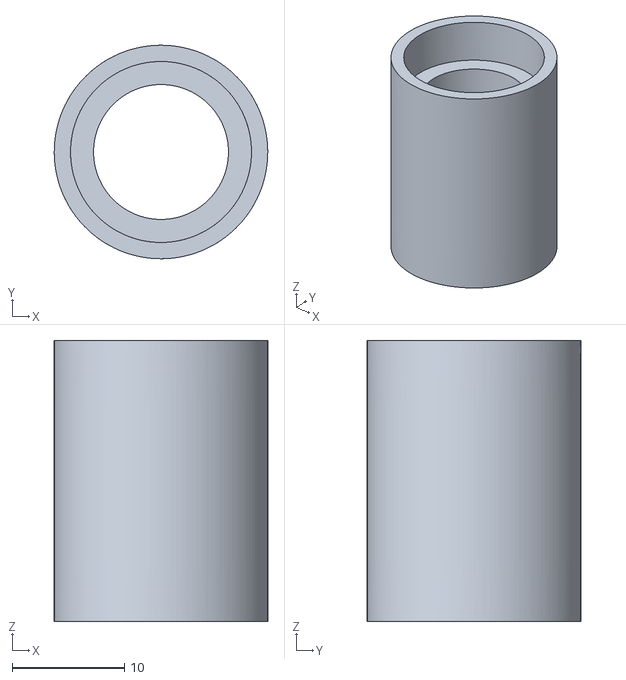
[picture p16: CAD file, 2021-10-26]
3_Files/2_3D CAD/3D CAD Parts/PolyJet/Trailing wheel/Trailing_wheel_Hard.stl
19.0 x 19.0 x 25.0

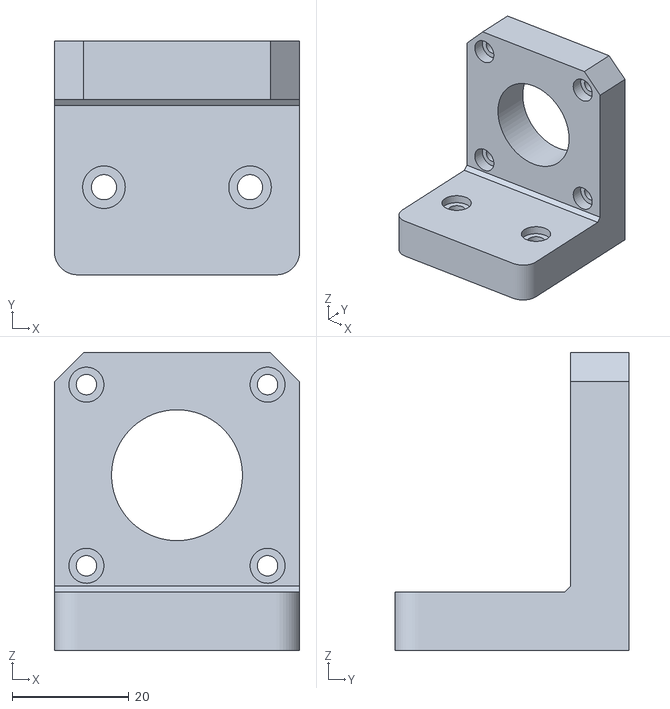
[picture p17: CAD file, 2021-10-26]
3_Files/2_3D CAD/3D CAD Parts/Filament/Motor_mount.stl
42.0 x 40.0 x 51.0

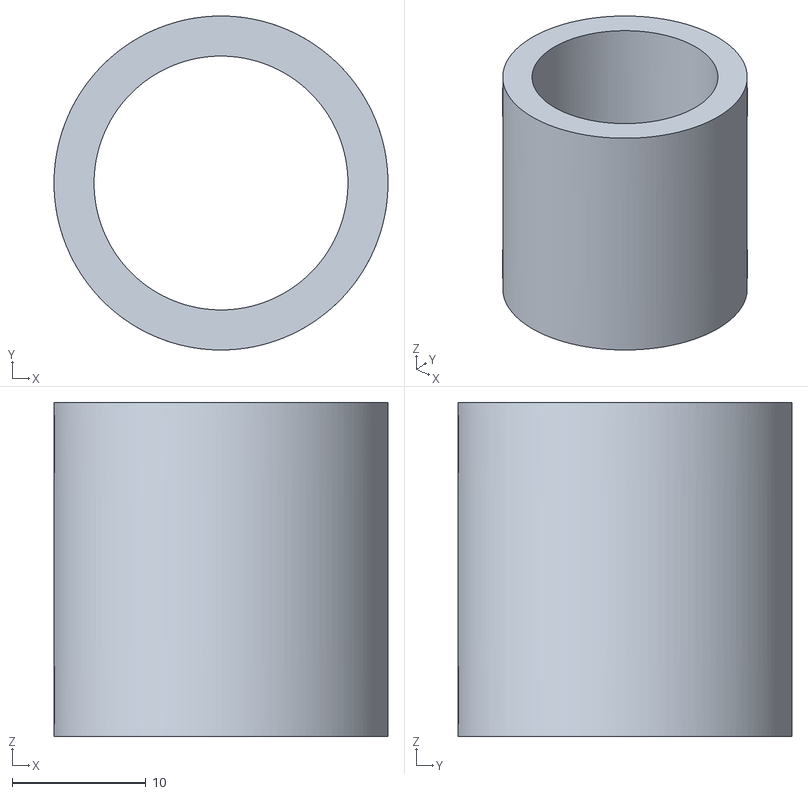
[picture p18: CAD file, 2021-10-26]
3_Files/2_3D CAD/3D CAD Parts/PolyJet/Drive wheel/Drive_wheel_Soft.stl
25.0 x 25.0 x 25.0

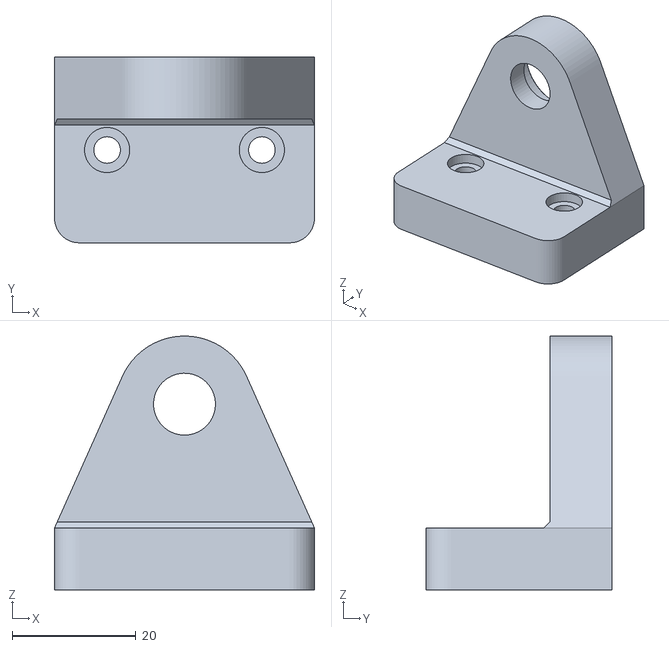
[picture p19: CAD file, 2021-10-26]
3_Files/2_3D CAD/3D CAD Parts/Filament/Motor_Axle_Mount_2.stl
42.0 x 30.0 x 41.0

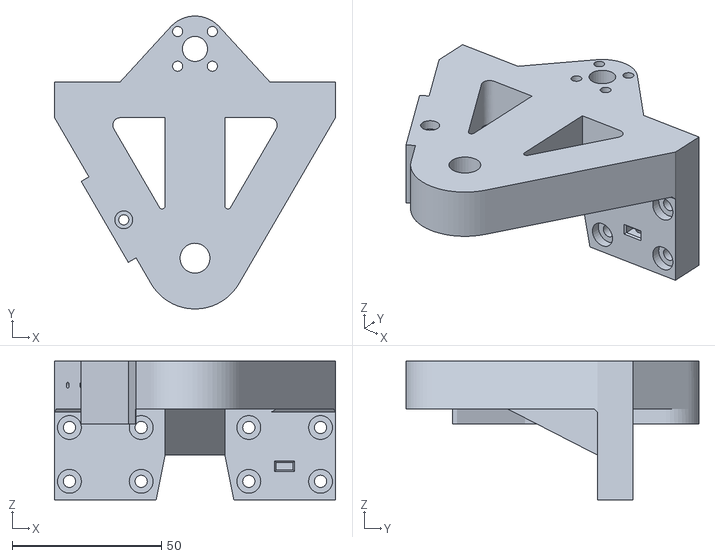
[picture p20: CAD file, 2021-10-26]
3_Files/2_3D CAD/3D CAD Parts/Filament/Table_upper_part.stl
94.0 x 98.0 x 46.4

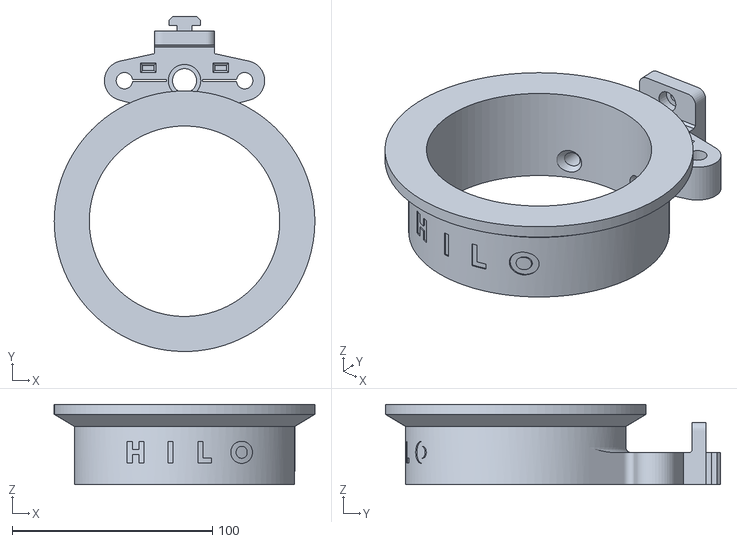
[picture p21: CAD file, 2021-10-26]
3_Files/2_3D CAD/3D CAD Parts/Filament/Spinnring.stl
130.0 x 167.1 x 40.0

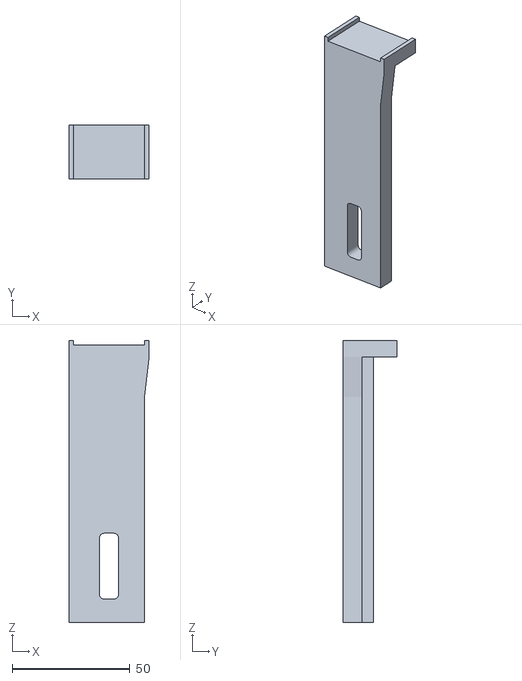
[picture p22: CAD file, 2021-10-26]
3_Files/2_3D CAD/3D CAD Parts/Filament/Hinge_stop.stl
34.2 x 23.0 x 120.0

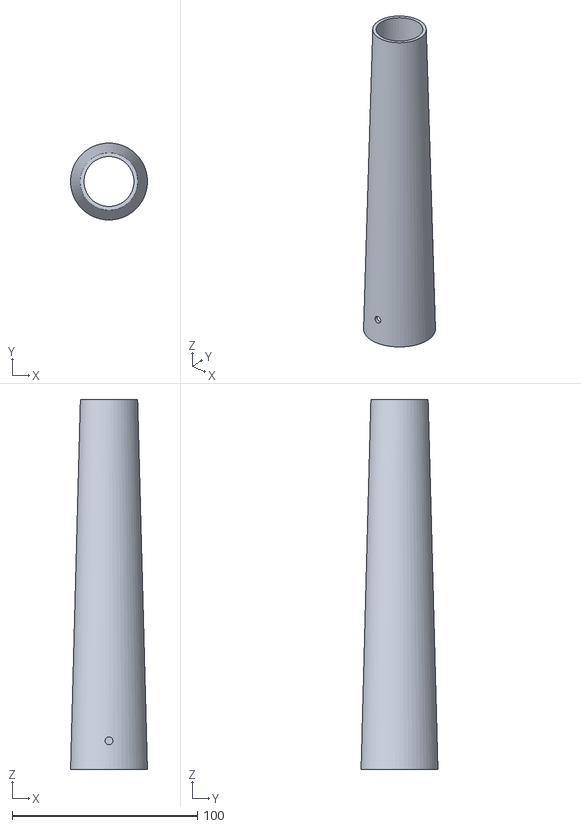
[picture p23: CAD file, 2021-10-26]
3_Files/2_3D CAD/3D CAD Parts/Filament/Spindle.stl
41.6 x 41.6 x 200.0

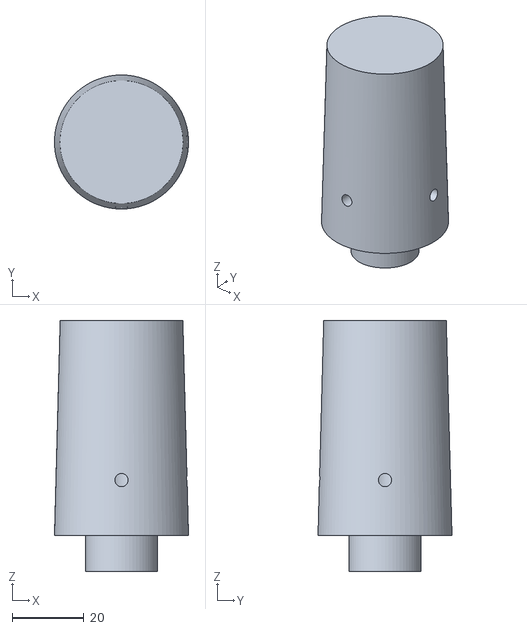
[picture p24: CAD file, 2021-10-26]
3_Files/2_3D CAD/3D CAD Parts/Filament/Spindle_carrier.stl
37.4 x 37.4 x 70.0

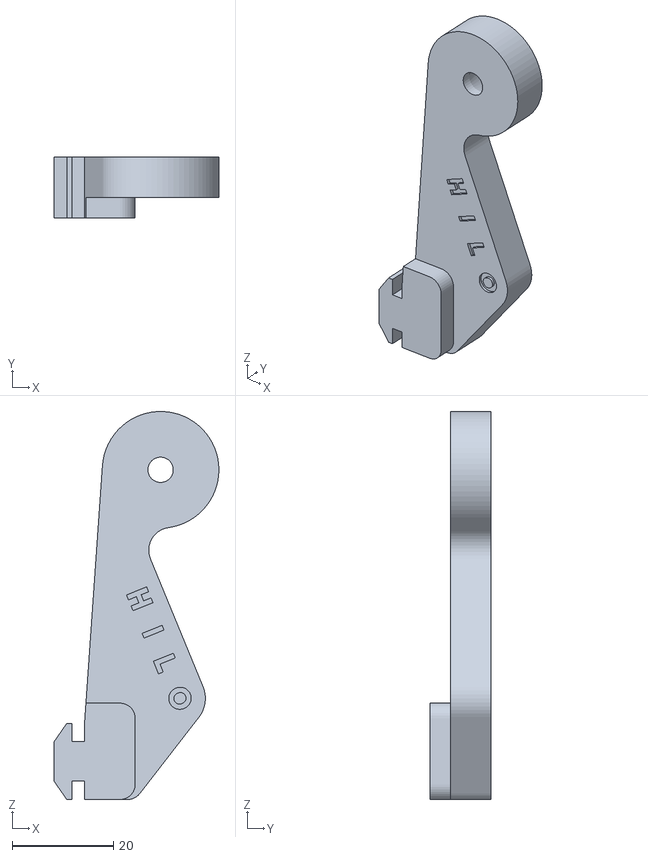
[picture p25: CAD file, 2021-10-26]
3_Files/2_3D CAD/3D CAD Parts/Filament/Yarn_guide_front.stl
32.5 x 12.0 x 76.5

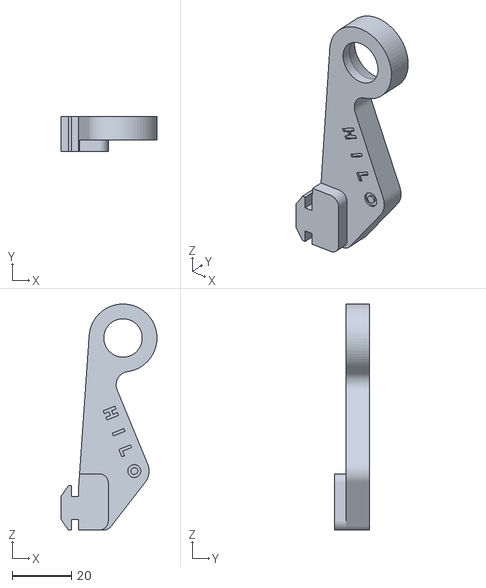
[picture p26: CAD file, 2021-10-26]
3_Files/2_3D CAD/3D CAD Parts/Filament/Yarn_guide_back.stl
32.5 x 12.0 x 76.5

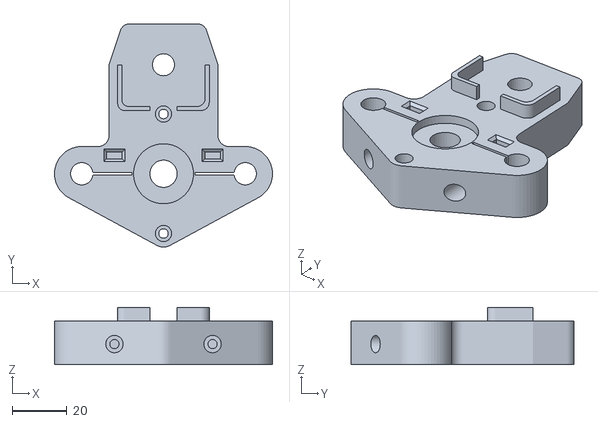
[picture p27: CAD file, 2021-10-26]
3_Files/2_3D CAD/3D CAD Parts/Filament/Elevator_lower_part.stl
80.0 x 81.9 x 21.0

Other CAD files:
3_Files/2_3D CAD/3D CAD Parts/PolyJet/Trailing wheel/Trailing_wheel_Soft.stl
3_Files/2_3D CAD/3D CAD Parts/Filament/Table_lower_part.stl
3_Files/2_3D CAD/3D CAD Parts/Filament/Yarn_outlet.stl
3_Files/2_3D CAD/HILO Spinning Machine/Fusion/210629_HILO_Top_Assembly v14.f3d

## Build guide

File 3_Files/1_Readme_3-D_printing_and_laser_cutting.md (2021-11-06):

#What to consider when 3-D printing and laser cutting?
 
All 3D printing and laser cutting parts have their own folder, please download both folders for the correct files. You can either produce the parts yourself by going to a FabLab or university in your city – or order them online.
 
## FabLab

FabLabs are fabrication laboratories that offer small-scale personal fabrication tools. Here you can search for the closest FabLab worldwide: https://www.fablabs.io/labs/map. Make sure you are prepared, when going to a FabLab! Bring your USB stick with all files on both folders for 3-D and laser cutting. Call or email them ahead to get prices (material, time of usage, etc.), opening hours and support.
 
## Online

There are also online websites where you can send the files to print and produce the parts. They are a bit more expensive than doing it on the spot, but more convenient.  
3-D printing: https://www.shapeways.com/ ; https://i.materialise.com/en
Laser cutting: https://cotter.co

## Data files

The laser cutting parts are in eps format, we created them with Adobe Illustrator.
The 3-D files are in stl format and are compatible with any 3D printer, you will also find the machine drawing as Fusion file.

## 3D Printing

1. Polyjet
Polyjet printing enables you to choose from a wide range of mechanical properties—from flexible to rigid. The wheels are printed in two properties, the outside (black) in max. soft and the inside (white) in max. hardness 

		Suggested printer:
		Stratasys Objet260 Connex 3 

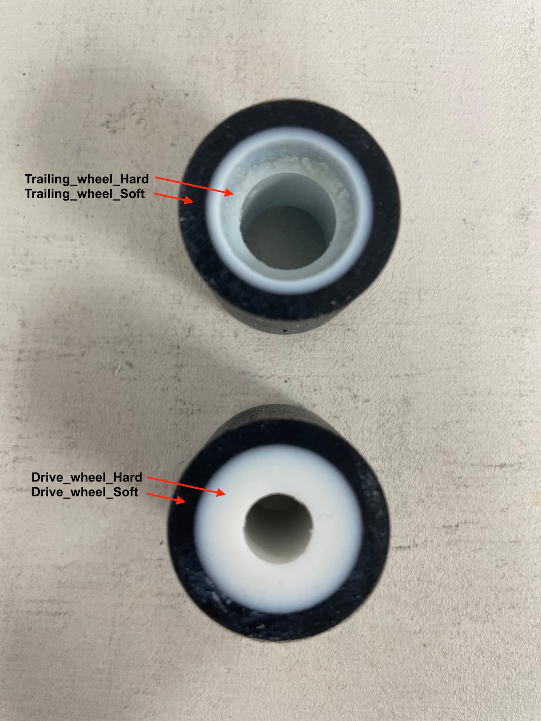
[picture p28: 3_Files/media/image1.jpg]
Printer
  

2. Filament
Printer: Original Prusa MK3S, Multimaker, Craftbot or similar
Material: PLA
Filament diameter: 1,75 mm
Infill: 15%

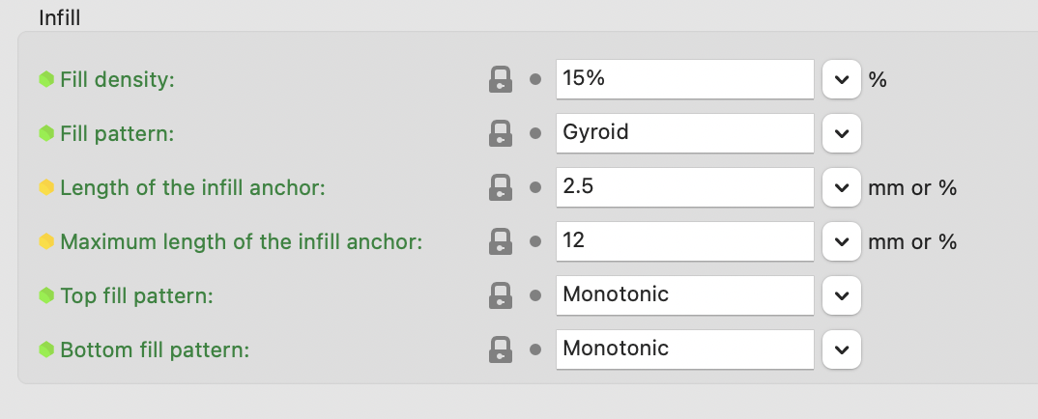
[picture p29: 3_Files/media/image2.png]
Printer settings


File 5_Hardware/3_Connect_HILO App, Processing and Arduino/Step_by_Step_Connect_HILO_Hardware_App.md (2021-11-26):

# What programs to download to run the HILO App? 

Please download the free programs “Processing” and “Arduino” on the following websites. We use them to run the HILO App and they are all connected with each other. 

* Processing: https://processing.org/download/
* Arduino: https://www.arduino.cc/en/Main/Software

## How to start with Arduino? 
After you follow the step by step electronic instructions you are ready to activate the Arduino Mega and upload HILO_App 

Follow the next steps →

    1. Connect the USB cable in the Arduino Mega Board and in the Computer  

Arduino Mega  

Laptop  

    2. To Start with the Arduino software → open the HILO Firmware in the folder HILO_App  

    3. Please double click CommandParser.ino to open it →  

    4. Now you see all the four tabs of the HILO_Firmware in Arduino program   

Laptop  

    5. Go to tools → select the Arduino Board → Arduino/Genuio Mega or Mega 2560
 
    6. Go to tools → select the Port USBmodem→  

    7. Press on the play button to upload the Software in the Arduino (take’s some seconds to upload it!!). 
	   Once the Arduino is uploaded in our Mega board you don't have to do it again ;) 
	   It stays there forever till you upload another project on it.   

Remember to connect always the USB cable with the Arduino Mega Board and computer, as in picture 1 

    8. Please wait until the message Done uploading in the bottom of the window appears 

    9. You uploaded the code successfully and now you can close the Arduino in your computer and we will start with Processing.

## How to activate Processing? 
After you install Processing please follow the next steps to open the HILO_App →

    10. Remember to leave the USB connected in the Arduino Mega Board with the computer. 
	    To Start with Processing software → open the folder HILO_App in the folder HILO_App  

    11.  Double click on any document in the folder 

    12. The Processing software opens automatically and the Hilo_App opns in your computer→ 
	    please click on the run/play button to start the HILO App interface. (take’s a few seconds to open the app)

Processing

    13. A new window appears on your screen. 
		This is the HILO App, with this interface you can control the Spinning Machine and start spinning.

    14. Click on the word HILO to start the app →  

HILO

    15. You can select a working mode Spin or Twist→

HILO

    16. Choose the material of the fibers you want to spin → 

HILO

    17. In this adjustment preview you can set the yarn thickness and twist intensity in the sliders on the right menu. 
		You see a preview of your yarn in the left window. When ready to produce just press the PLAY button. →  

HILO

    18. The software will automatically ask you to connect to the HILO machine by USB. 
		Choose the USB port that contains “usbmodem” in the file name (e.g. /dev/tty.usbmodemFD121). → 

HILO

    19. After selecting the correct port you will come back to the adjustment preview from before. 
		Here you can change settings, produce and adjust directly by pressing PLAY and PAUSE.  → 
HILO

    20. Please Calibrate the Motors before you start working with the Spinning Machine
        Check this link to calibrate the Driver Modules 
        https://www.youtube.com/watch?v=VyHhRsN7Wr0

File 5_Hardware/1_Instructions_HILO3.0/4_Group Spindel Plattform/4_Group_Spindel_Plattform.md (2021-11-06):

# Description of Groups Components Description

## Group: Spindel Plattform

|Type |Component |Amount|Description|Link|
|:---|:---|:---|:---|:---|
|Hardware|Cylindrical screw M3x10|1|ISO 4762 M3 x 10|Hardware store|
|Hardware|Cylindrical Screw M3x12|4|ISO 4762 M3 x 12|Hardware store|
|Hardware|Cylindrical Screw M3x30|16|ISO 4762 M3 x 30|Hardware store|
|Hardware|Nut M3|16|ISO 4032 - M3|Hardware store|
|Hardware|Spacer Sleeve|2|ISO 845|Hardware store|
|Hardware|Trapezoidal Screw Nut T8|1||[Link](https://www.amazon.com/ReliaBot-300mm-Thread-Starts-Printer/dp/B07B63CVSJ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(Acme%2Bthread%2C%2B2%2Bmm%2Bthread%2Bpitch%2C%2B4%2Bstart%2C%2B8%2Bmm%2Bpitch%29%2Bfor%2B3D%2Bprinters%2Band%2BCNC%2Bmachine%2BZ-axis&qid=1635337457&sr=8-1&th=1)|
|Hardware|Round Metal Bar|1|D: 8 mm L: 90 mm|[Link](https://www.azurefilm.com/en/guides-8mm)|
|Hardware|Spindle|1|T8; L: 200 mm|[Link](https://www.amazon.com/ReliaBot-300mm-Thread-Starts-Printer/dp/B07B63CVSJ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(Acme%2Bthread%2C%2B2%2Bmm%2Bthread%2Bpitch%2C%2B4%2Bstart%2C%2B8%2Bmm%2Bpitch%29%2Bfor%2B3D%2Bprinters%2Band%2BCNC%2Bmachine%2BZ-axis&qid=1635337457&sr=8-1&th=1)|
|Hardware|Linear bearing|2|SC8UU for 8mm|[Link](https://www.amazon.de/-/en/Length-SC8UU-Linear-Bearing-Bushing/dp/B077KQR45N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)|
|Hardware|Bearing|2|8x16x5 mm|[Link](https://www.azurefilm.com/en/bearing.2)|
|Hardware|GT2 Pulley 20 teeth|1|20 teeth GT2 timing pulley 8mm|[Link](https://www.azurefilm.com/en/20-or-16-teeth-gt2-timing-pulley)|
|Hardware|GT2 Pulley 40 teeth|1|40 teeth GT2 timing pulley 5mm|[Link](https://www.azurefilm.com/en/gt2-timing-pulley-8mm-40-teeth)|
|Hardware|Closed Belt Pulley |1|6 mm Length: 150m|[Link](https://www.amazon.de/gp/product/B075744P4Z/ref=ppx_yo_dt_b_asin_title_o03_s00?ie=UTF8&psc=1)|
|Printed Parts|Table lower part|1|PLA Filament 175|More specifications in document 1_Readme_ 3-D printing and laser cutting|
|Printed Parts|Table upper part|1|PLA Filament 175|More specifications in document 1_Readme_ 3-D printing and laser cutting|
|Printed Parts|Spindle|1|PLA Filament 175|More specifications in document 1_Readme_ 3-D printing and laser cutting|
|Printed Parts|Spindle Carrier|1|PLA Filament 175|More specifications in document 1_Readme_ 3-D printing and laser cutting|
|Electronics|Nema 17 Stepper Motor|1|Size: 42x42x39mm 1.5 A 12 V 39 mm 4-Wire 1.8 Deg Stepper Motor with 1 M Wire|[Link](https://www.azurefilm.com/en/ma-17-stepper-motor.2)|

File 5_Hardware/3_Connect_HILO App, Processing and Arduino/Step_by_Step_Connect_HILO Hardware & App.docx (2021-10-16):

What programs to download to run the HILO App?

Please download the free programs “Processing” and “Arduino” on the following websites. We use them to run the HILO App and they are all connected with each other.

Processing: https://processing.org/download/

Arduno: https://www.arduino.cc/en/Main/Software

How to start with Arduino?

After you follow the step by step electronic instructions you are ready to activate the Arduino Mega and upload HILO_App

Follow the next steps →

1. Connect the USB cable in the Arduino Mega Board and in the Computer

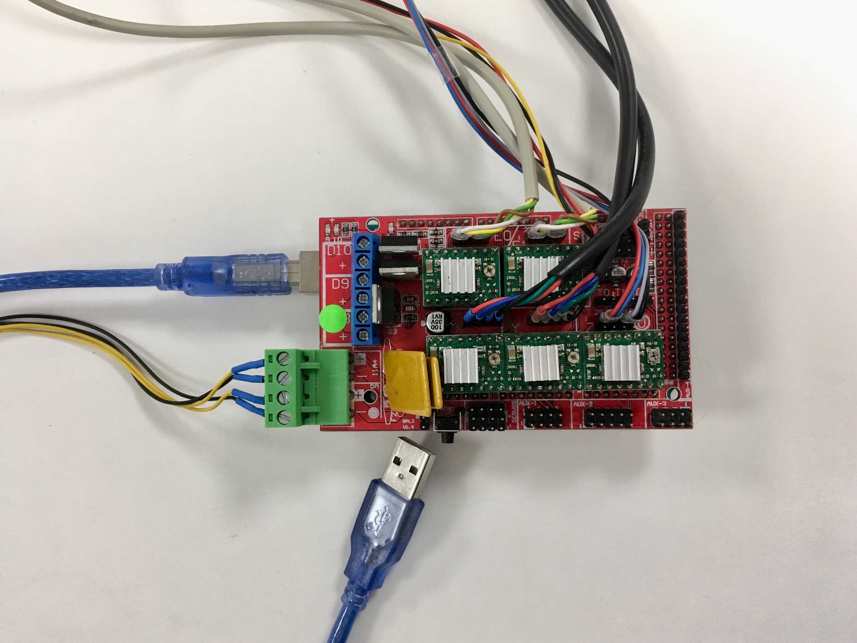
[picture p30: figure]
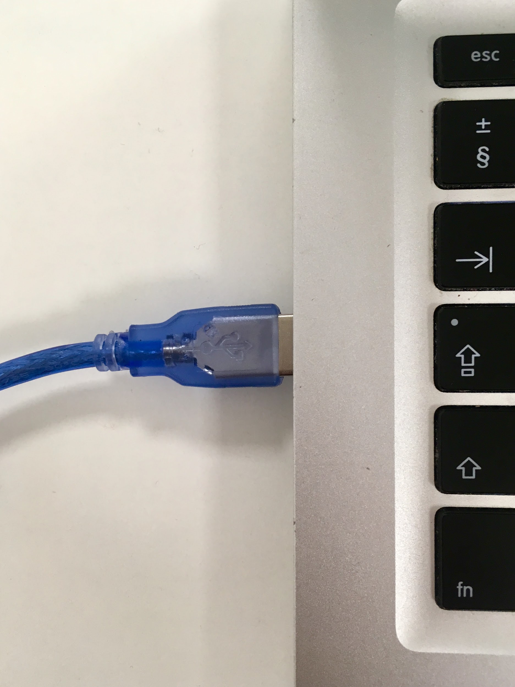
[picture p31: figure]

2. To Start with the Arduino software → open the HILO Firmware in the folder HILO_App
3. Please click double to open it →

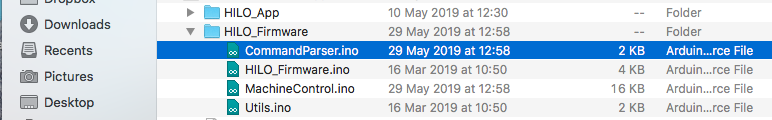
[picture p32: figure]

4. Now you see all the four tabs of the HILO_Firmware in Arduino program

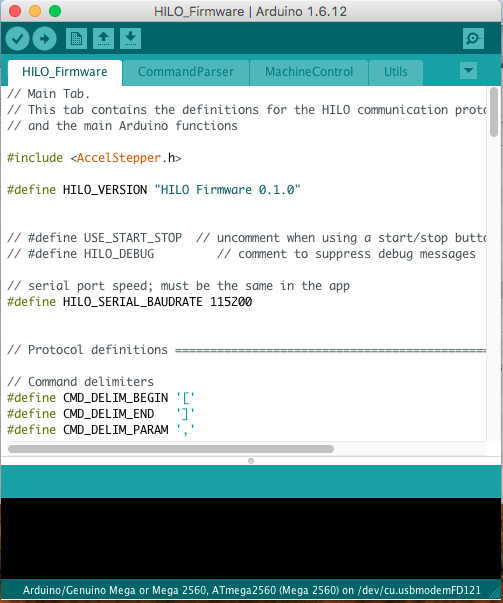
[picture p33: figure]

5. Go to tools → select the Arduino Board → Arduino/Genuio Mega or Mega 2560

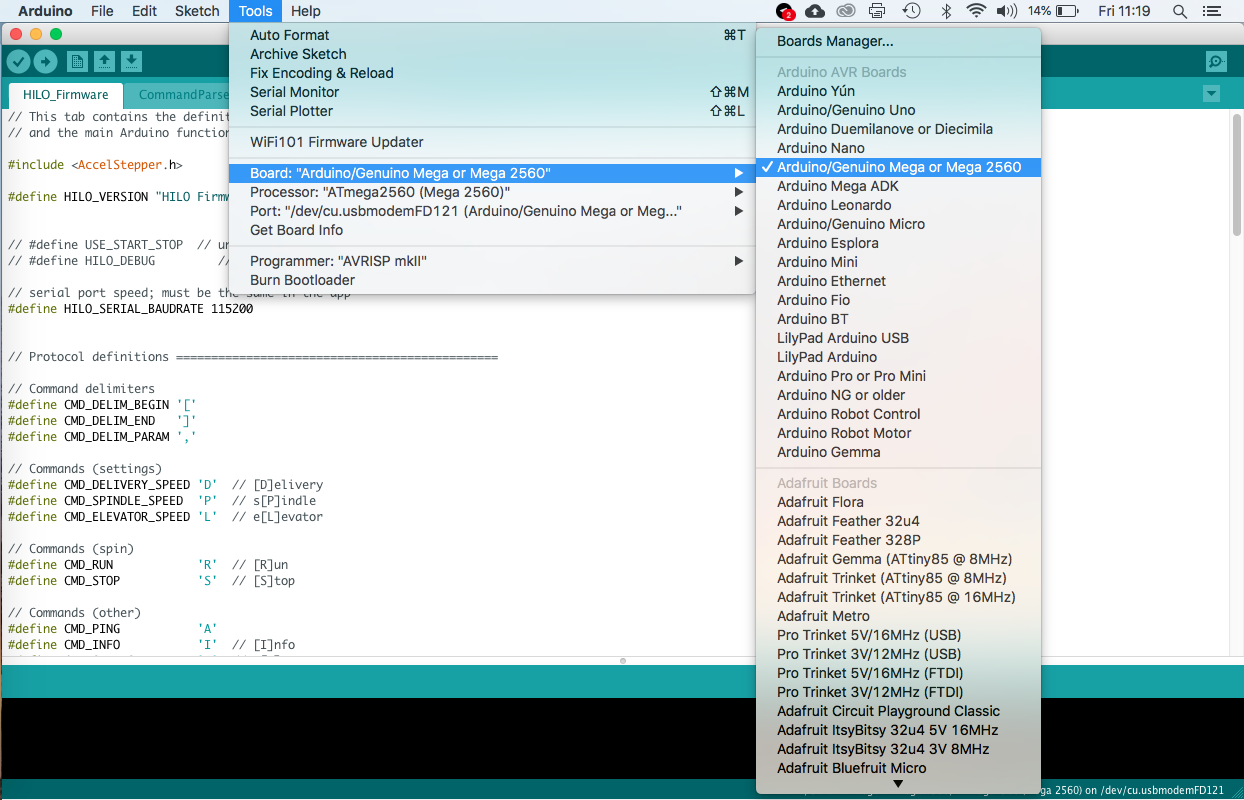
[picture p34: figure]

6. Go to tools → select the Port USBmodem→

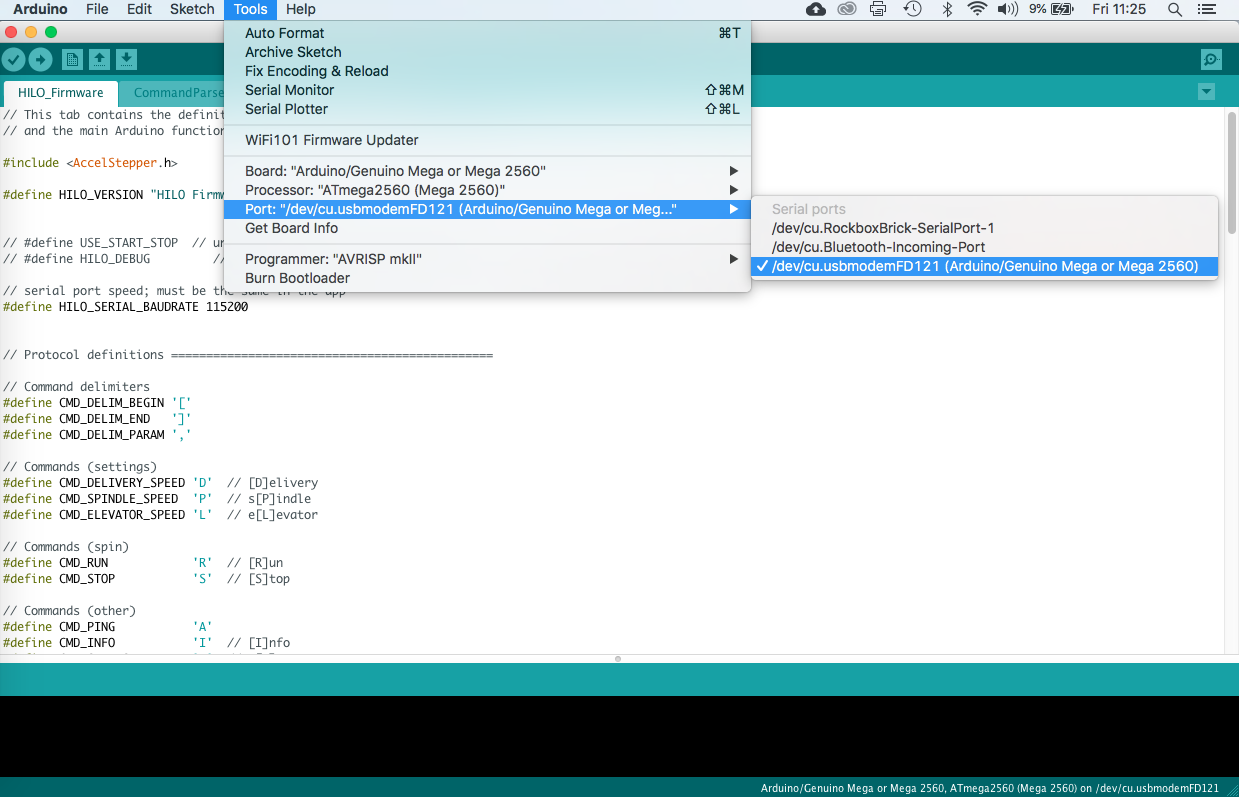
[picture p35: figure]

7. Press on the play button to upload the Software in the Arduino (take’s some seconds to upload it!!) Once the Arduino is uploaded in our Mega board you don't have to do it again ;) It stays there forever till you upload another project on it.

Remember to connect always the USB cable with the Arduino Mega Board and computer, as in picture 1

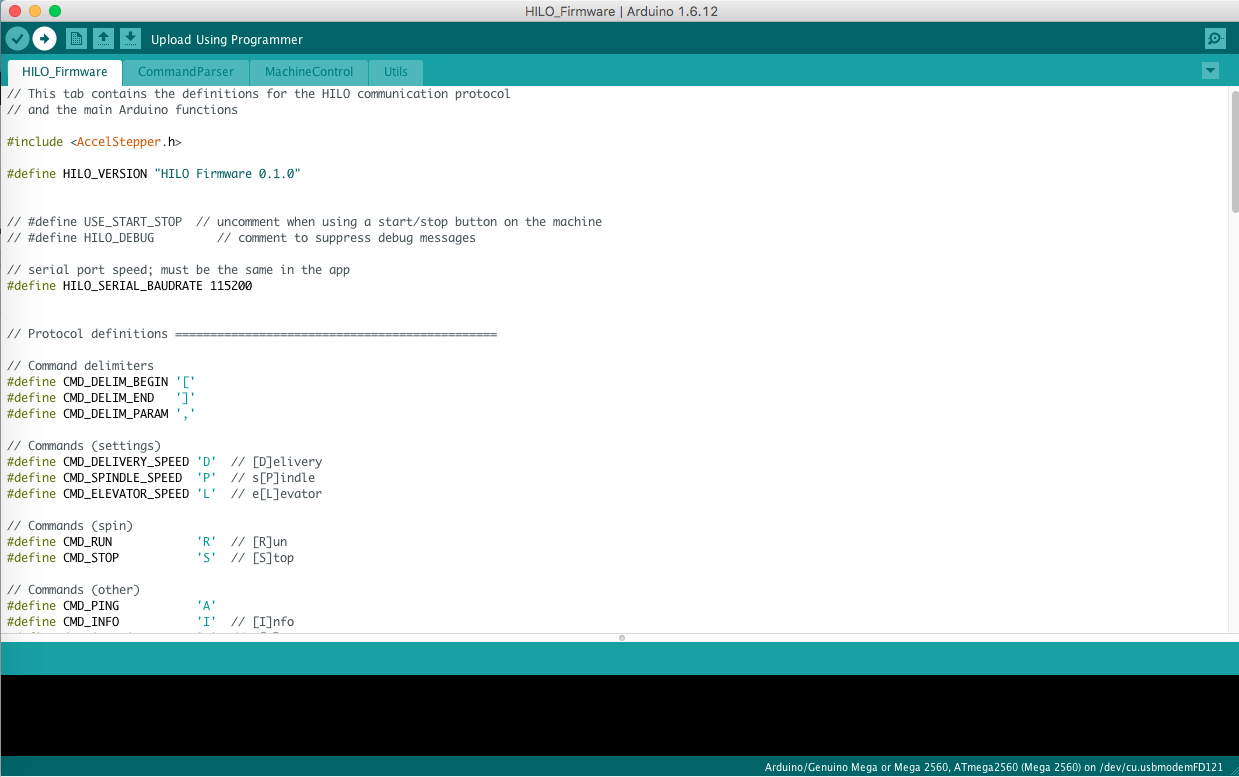
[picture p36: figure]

8. Please wait until the message Done uploading in the bottom of the window appears

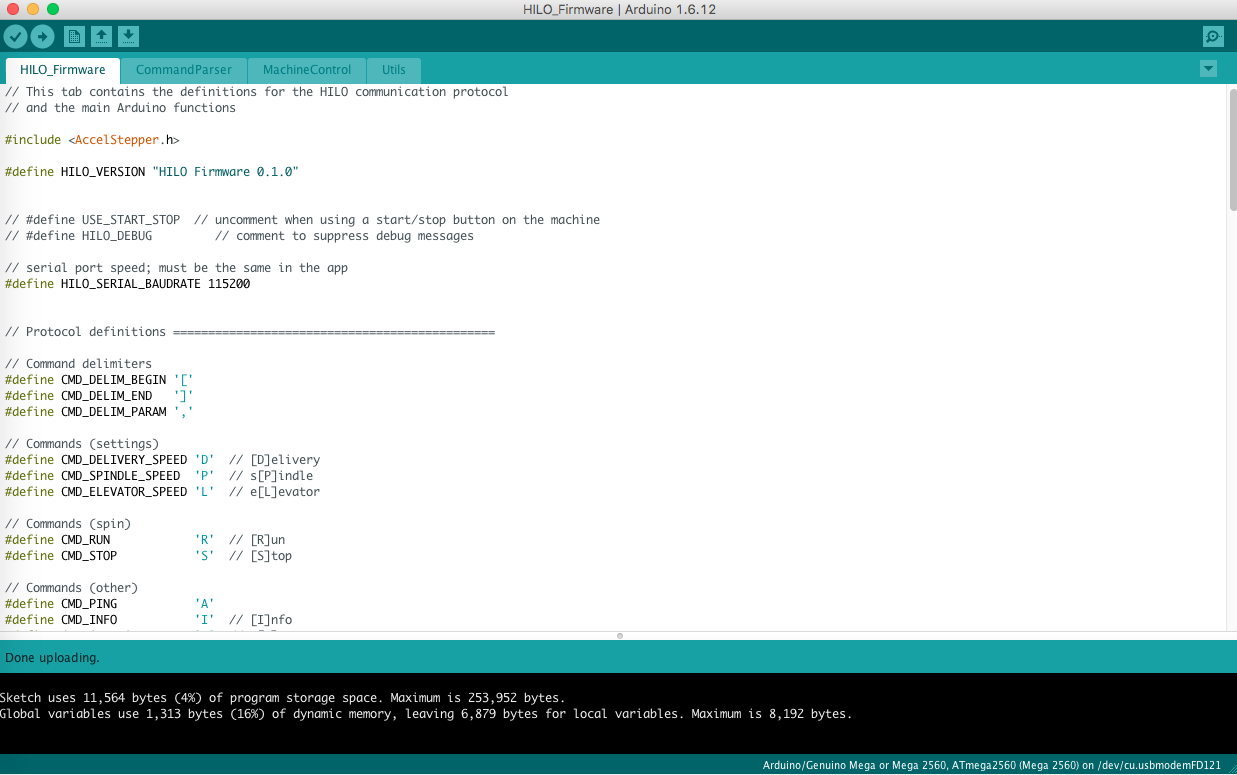
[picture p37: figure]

9. You uploaded the code successfully and now you can close the Arduino in your computer and we will start with Processing.

How to activate Processing?

After you install Processing please follow the next steps to open the HILO_App →

10. Remember to leave the USB connected in the Arduino Mega Board with the computer. To Start with Processing software → open the HILO_App in the folder HILO_App
11. Double click on any document in the folder
12. The Processing software opens automatically and the Hilo_App opns in your computer→ please click on the run/play button to start the HILO App interface. (take’s a few seconds to open the app)

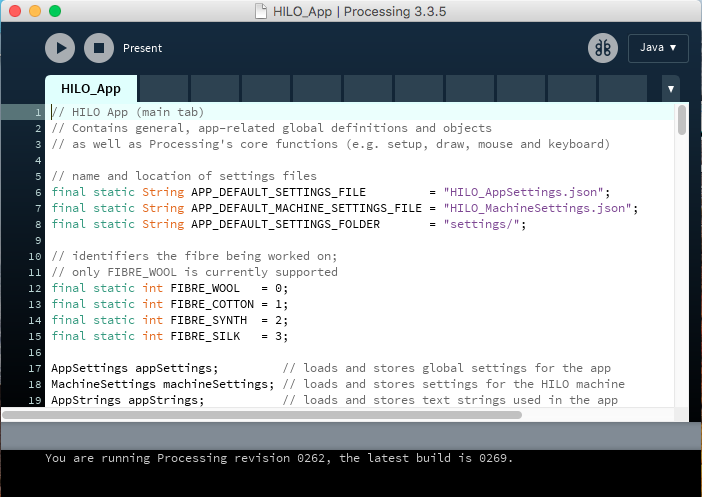
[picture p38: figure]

13. A new window appears on your screen. This is the HILO App, with this interface you can control the Spinning Machine and start spinning.
14. Click on the word HILO to start the app →

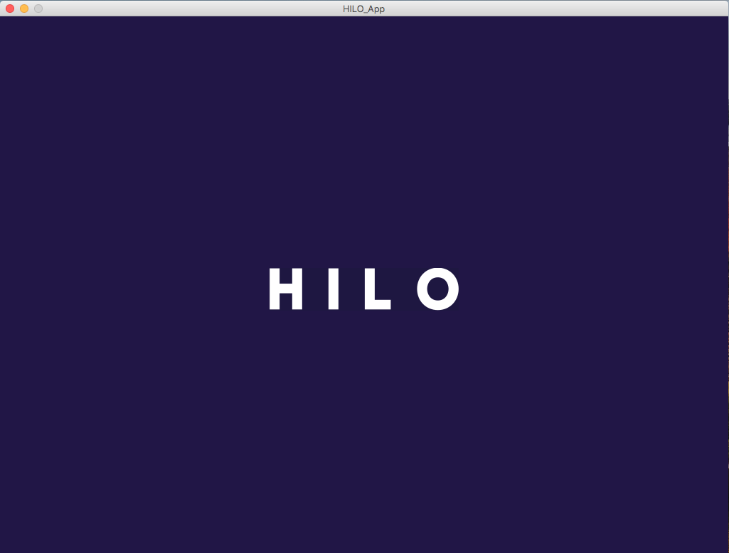
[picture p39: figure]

15. You can select a working mode Spin or Twist→

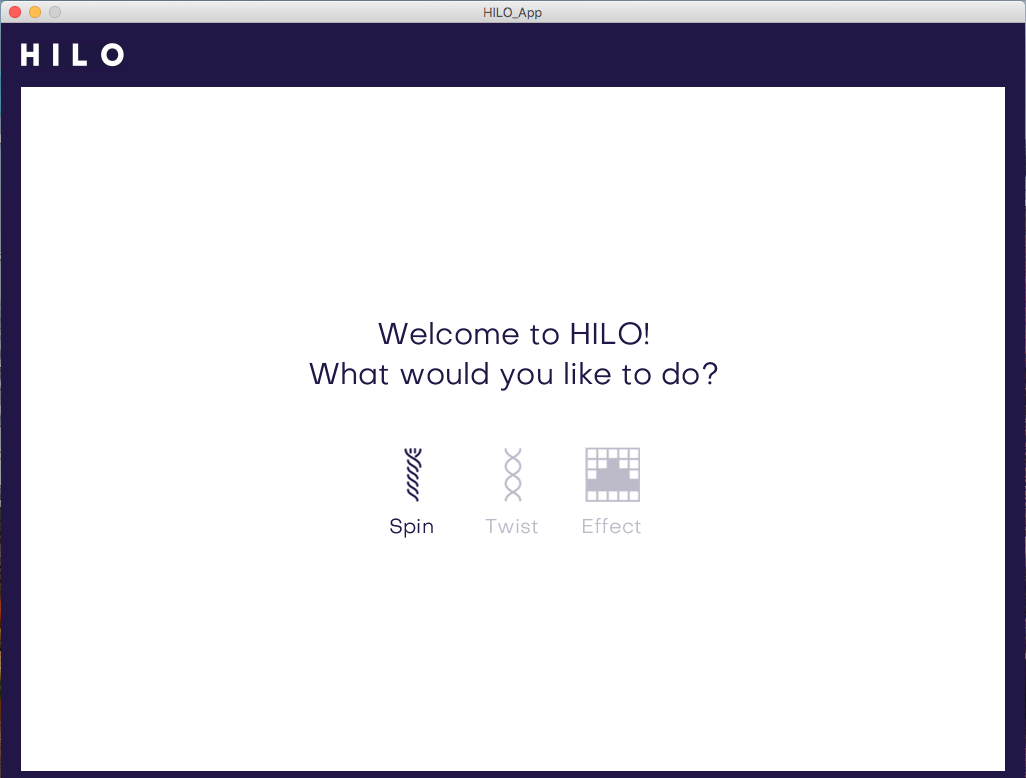
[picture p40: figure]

16. Choose the material of the fibers you want to spin →

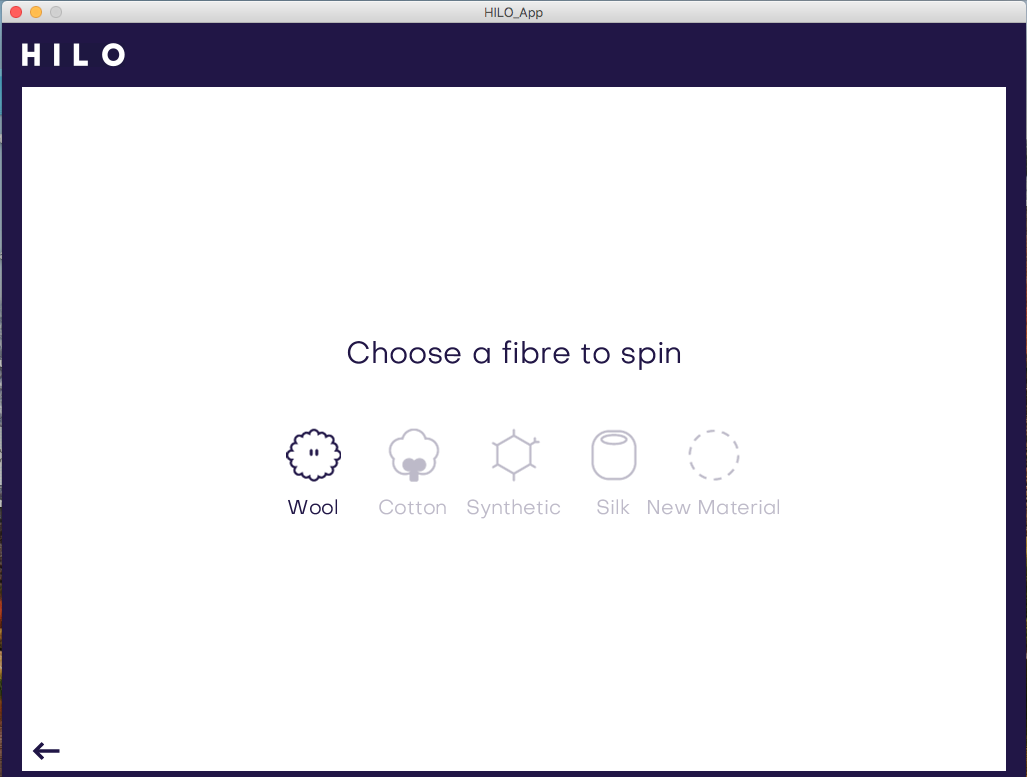
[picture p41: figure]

17. In this adjustment preview you can set the yarn thickness and twist intensity in the sliders on the right menu. You see a preview of your yarn in the left window. When ready to produce just press the PLAY button. →

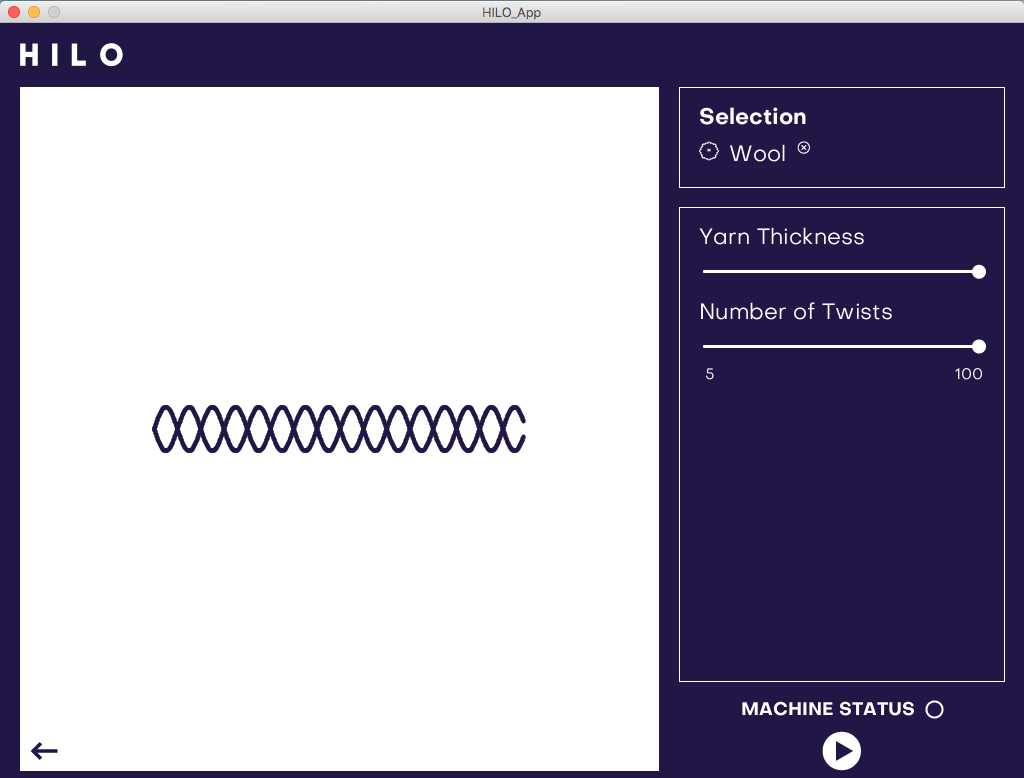
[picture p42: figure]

18. The software will automatically ask you to connect to the HILO machine by USB. Choose the USB port that contains “usbmodem” in the file name (e.g. /dev/tty.usbmodemFD121). →

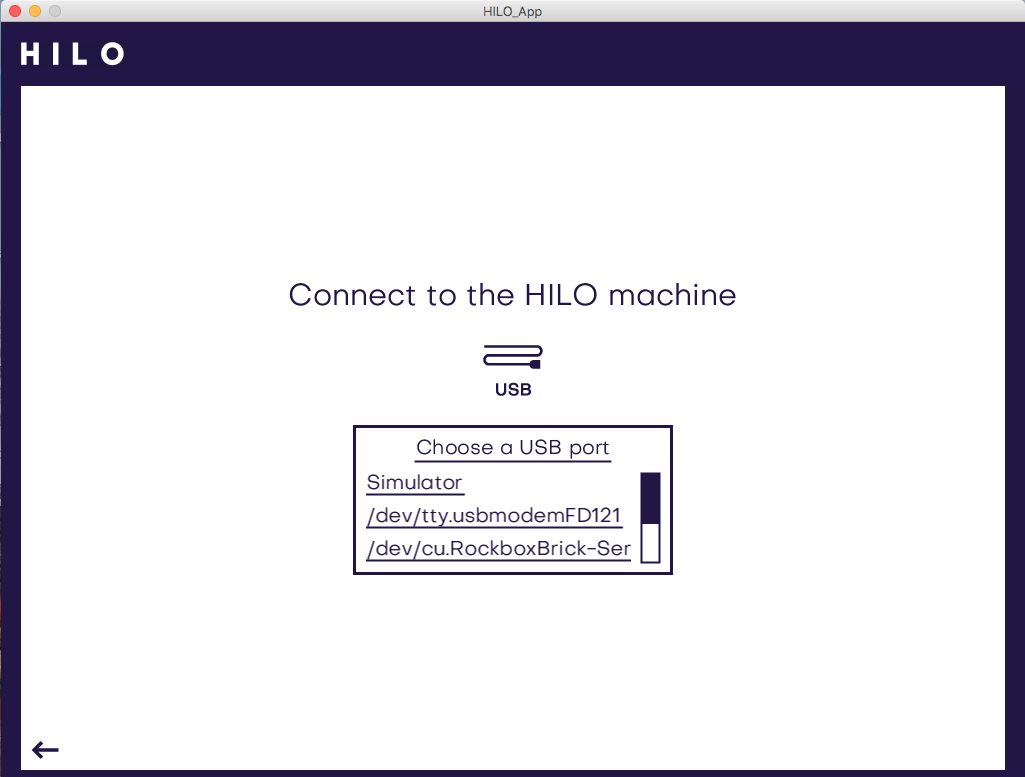
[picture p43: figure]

19. After selecting the correct port you will come back to the adjustment preview from before. Here you can change settings, produce and adjust directly by pressing PLAY and PAUSE. →

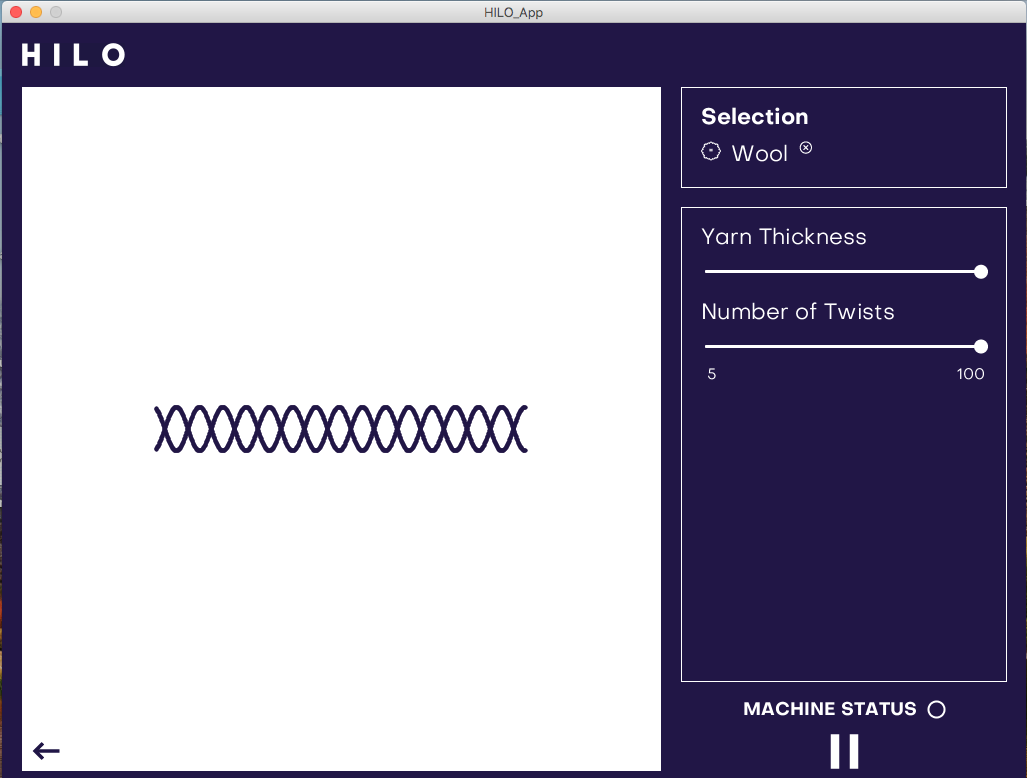
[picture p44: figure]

Step_by_Step_Connect_HILO Hardware & App_HILO Spinning Machine 3.0_14, July 2021

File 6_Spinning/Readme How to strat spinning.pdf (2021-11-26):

# How to start spinning

Before starting to spin, you have to check that the drive wheels are parallel. Make a double check that all of the screws are tightened enough. It is also recommended that the humidity in the room is approximately 60% to work with maschine.

## 1. Set the starting thread

put the scrap thread into the bottom of the bobbin, then attach the bobbin to the spindle carrier.

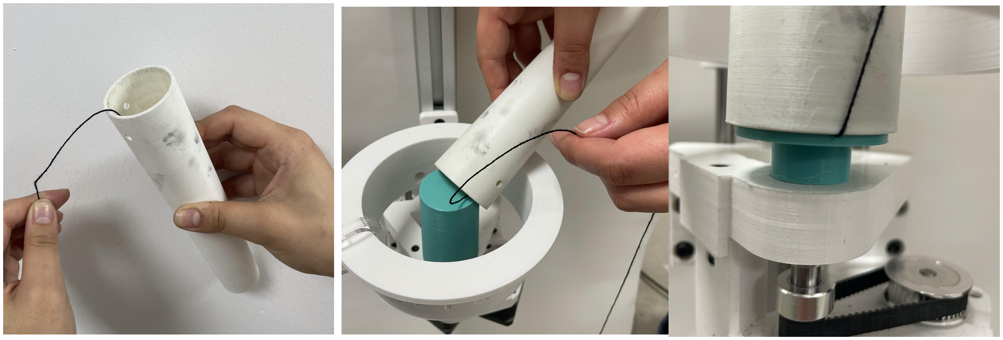
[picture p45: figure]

## 2. Wrap the yarn around the cone

Rotate the bobbin with the thread until the thread is on the same height as the traveler. Then put the thread through the hook.

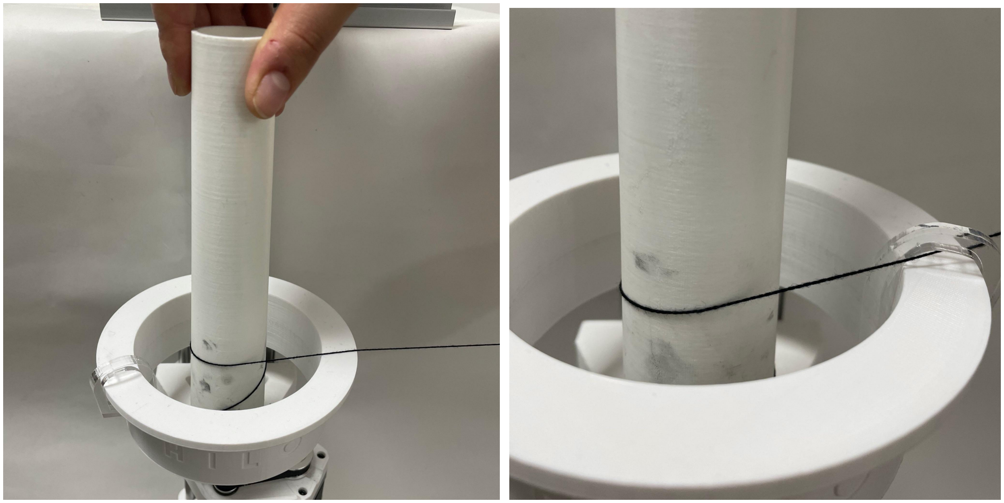
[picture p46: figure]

## 3. Pass the thread through the yarn traveler

pass the thread through the yarn outlet and pause it on the side.

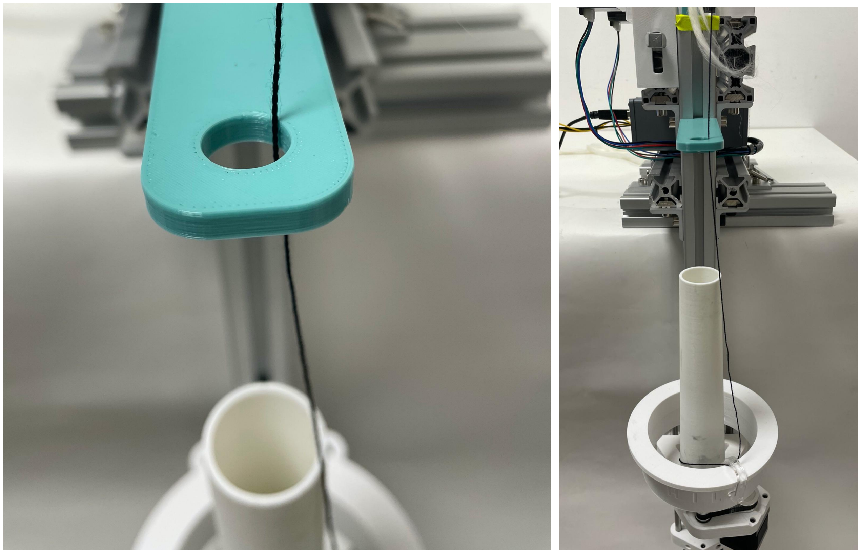
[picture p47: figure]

## 4. Prepare the roving (fibres)

Put the roving neatly behind the maschine. Make sure that the roving has no knot and there is nothing in the way.

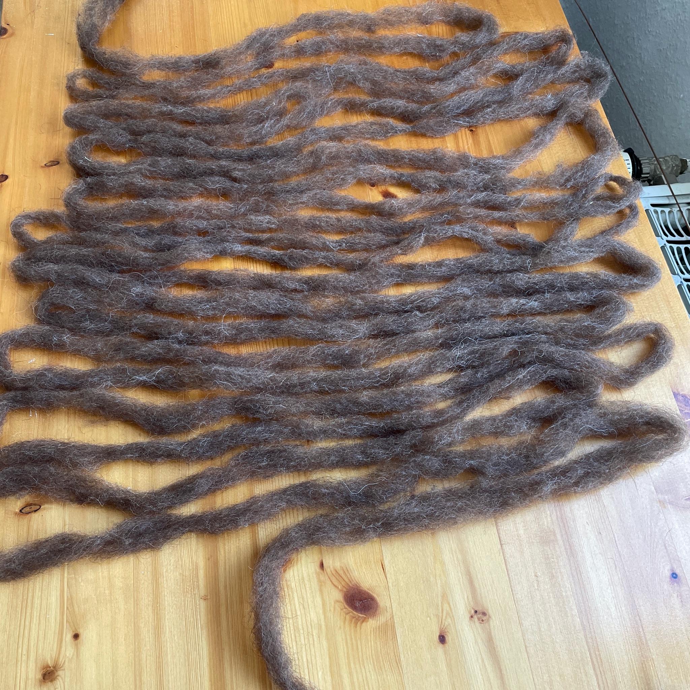
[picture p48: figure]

## 5. Set the roving (back)

Put the roving through the back Yarn Guide of the machine and guide them on the drive wheel to the front.

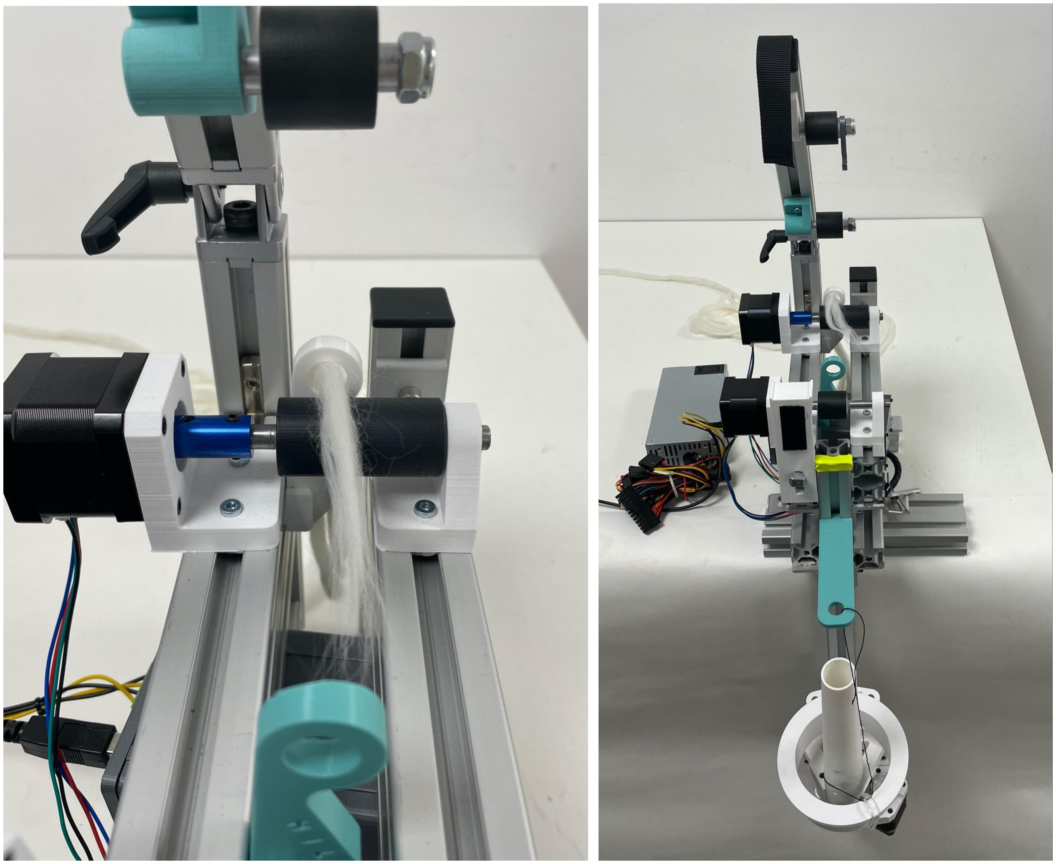
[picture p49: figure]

## 6. Set the roving (front)

Then put the roving through the front Yarn Guide and on the front drive wheel.

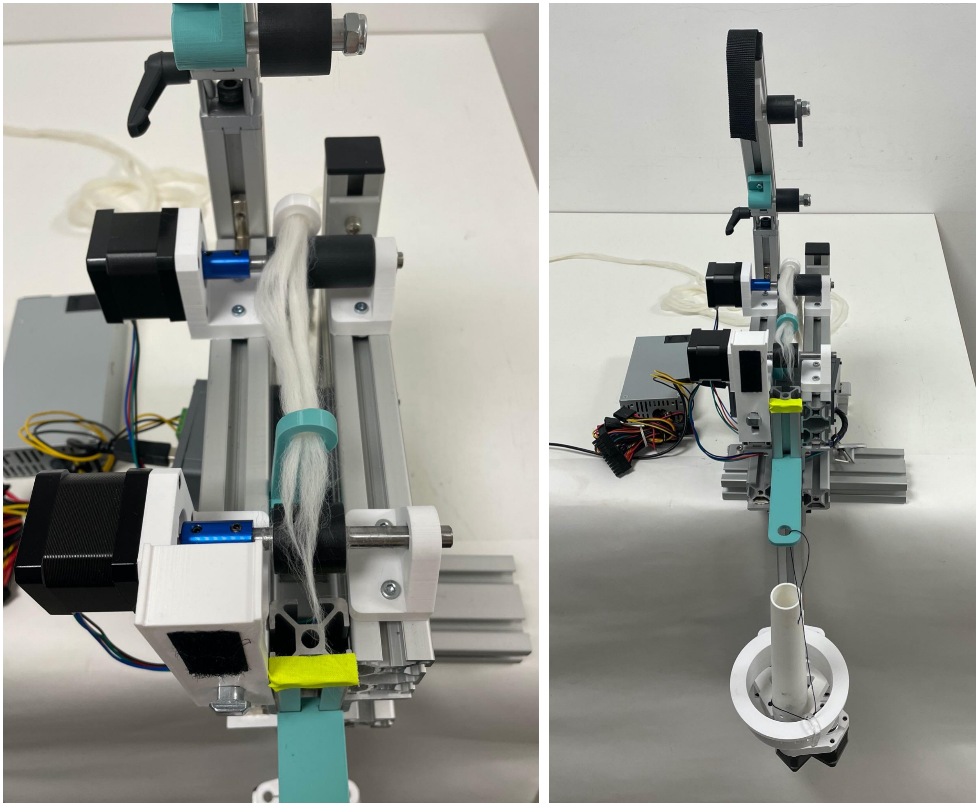
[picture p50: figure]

7. Put the thread and roving together.

Connect the thread coming from the hook with the roving and twist them a few times with your fingers.

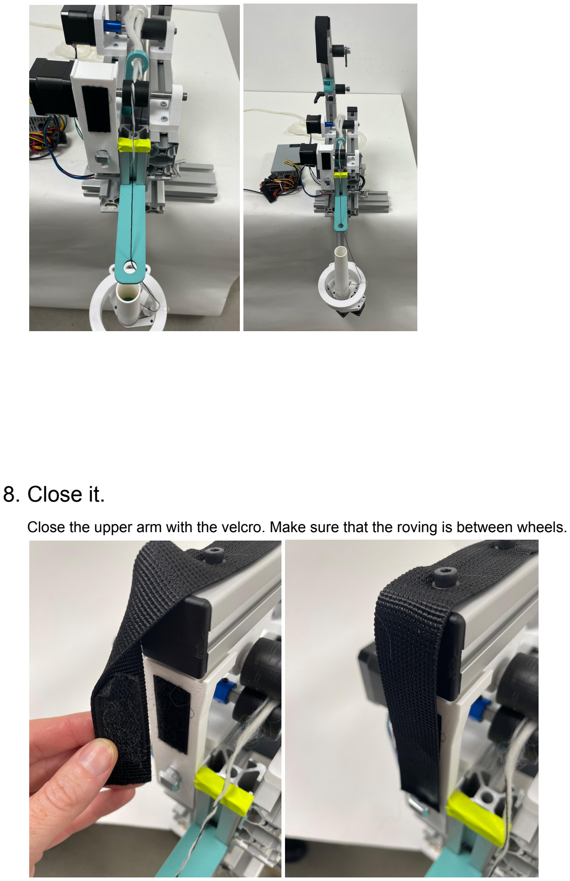
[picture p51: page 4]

8. Close it.

Close the upper arm with the velcro. Make sure that the roving is between wheels.

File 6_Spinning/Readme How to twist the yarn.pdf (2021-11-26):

# How to twist the yarns

Before starting to twist, you have to check that the drive wheels are parallel. Make a double check that all of the screws are tightened enough.

1. Prepare the yarns.

Put the yarns behind the maschine. Make sure that there is nothing in the way and the yarns come from the bobbin smoothly.

## 2. Set the yarn. (back drive wheels)

The yarns go through the back yarn guide and then above the back drive wheels. You don't use the back drive wheels and motor for twisting.

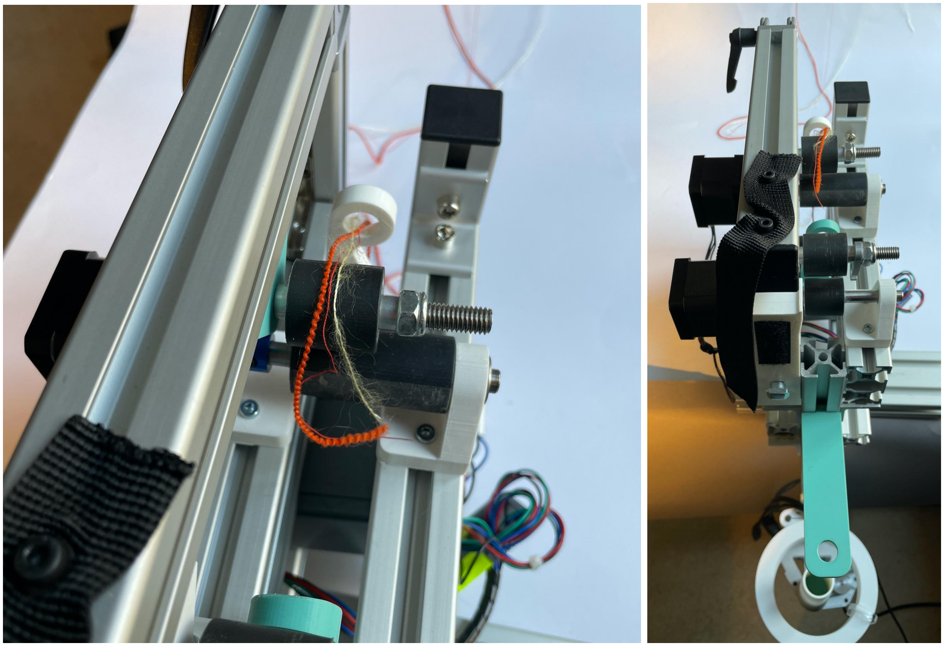
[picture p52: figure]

## 3. Set the yarn. (front drive wheels)

Pass the yarn through the front yarn guide and then between the wheels.

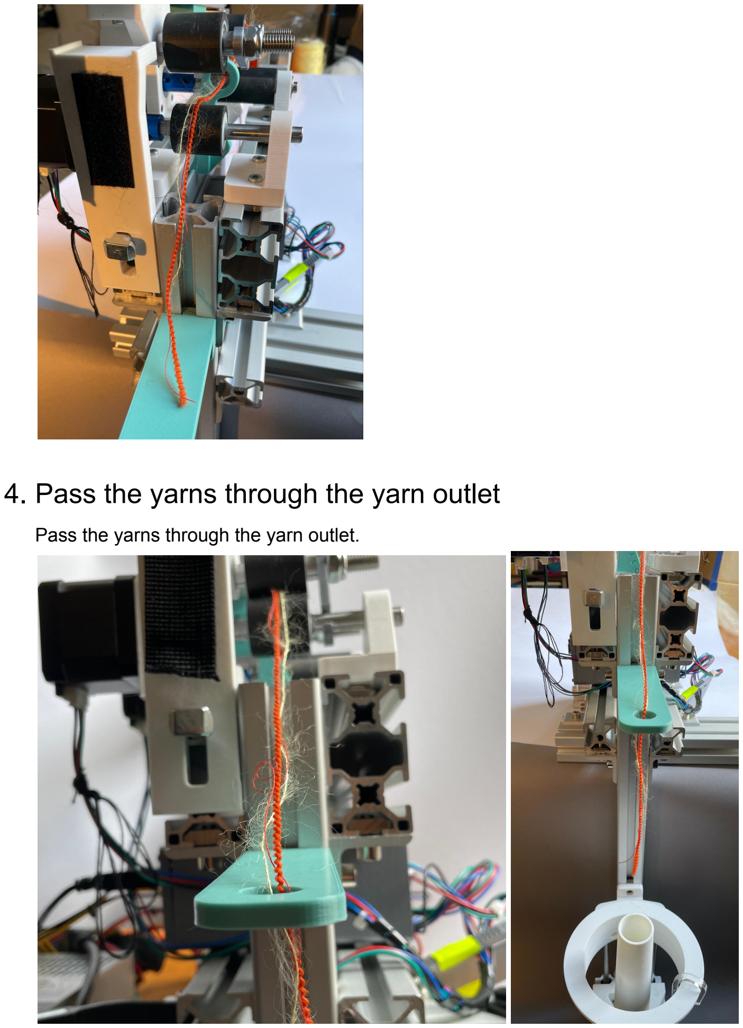
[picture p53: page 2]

## 4. Pass the yarns through the yarn outlet

Pass the yarns through the yarn outlet.

5. Put the yarns into the bobbin.

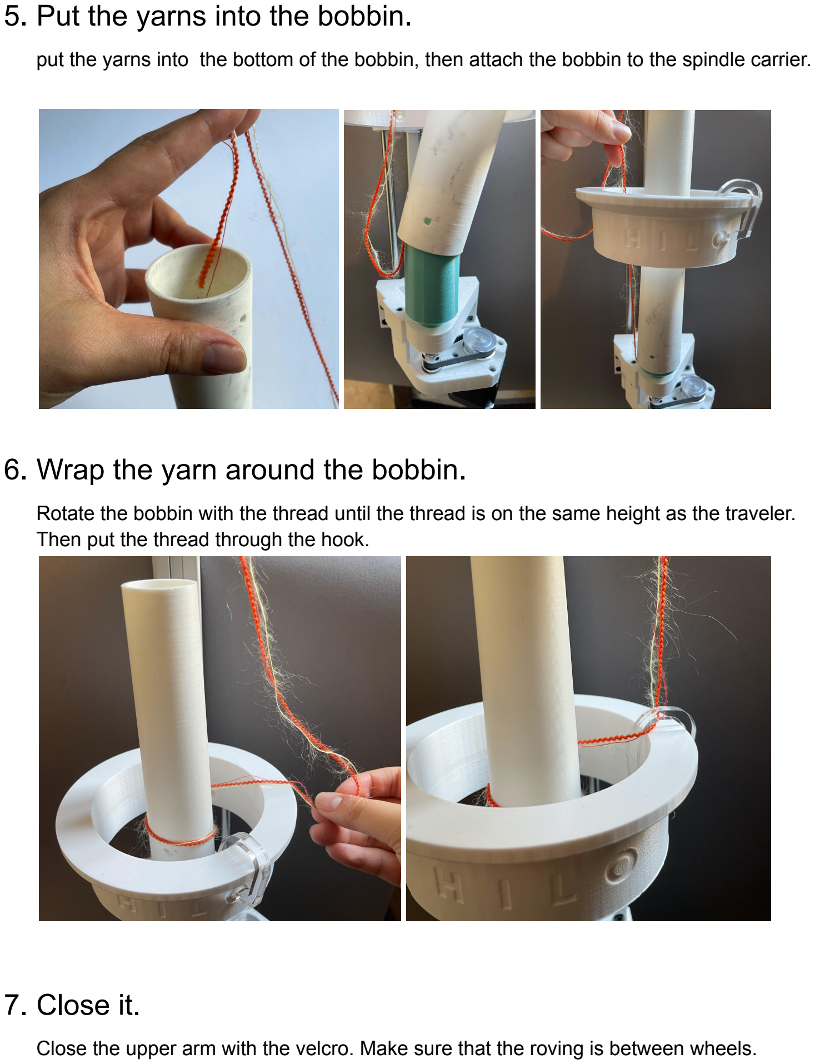
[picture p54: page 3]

put the yarns into the bottom of the bobbin, then attach the bobbin to the spindle carrier.

6. Wrap the yarn around the bobbin.

Rotate the bobbin with the thread until the thread is on the same height as the traveler. Then put the thread through the hook.

7. Close it.

Close the upper arm with the velcro. Make sure that the roving is between wheels.

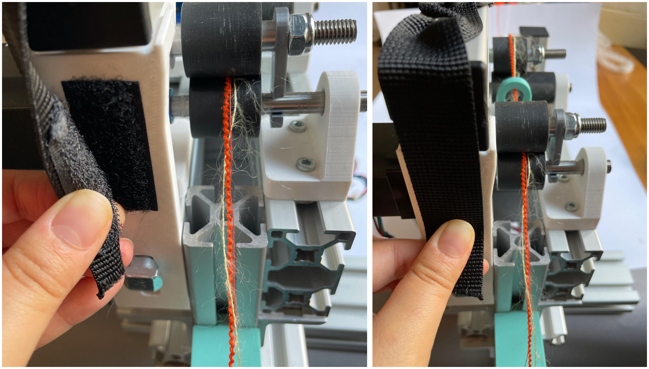
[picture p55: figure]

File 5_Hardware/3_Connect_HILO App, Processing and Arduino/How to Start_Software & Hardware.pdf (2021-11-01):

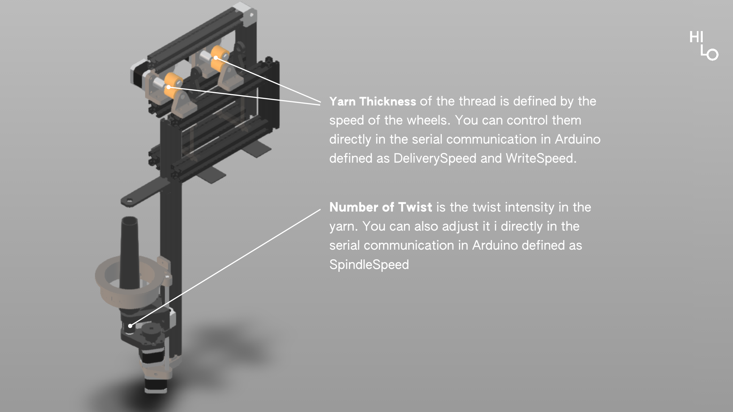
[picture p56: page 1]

Yarn Thickness of the thread is defined by the speed of the wheels. You can control them directly in the serial communication in Arduino defined as DeliverySpeed and WriteSpeed.

Number of Twist is the twist intensity in the yarn. You can also adjust it i directly in the serial communication in Arduino defined as SpindleSpeed

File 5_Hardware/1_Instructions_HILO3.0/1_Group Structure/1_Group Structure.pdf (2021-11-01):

# HILO SPINNING MACHINE 3.0

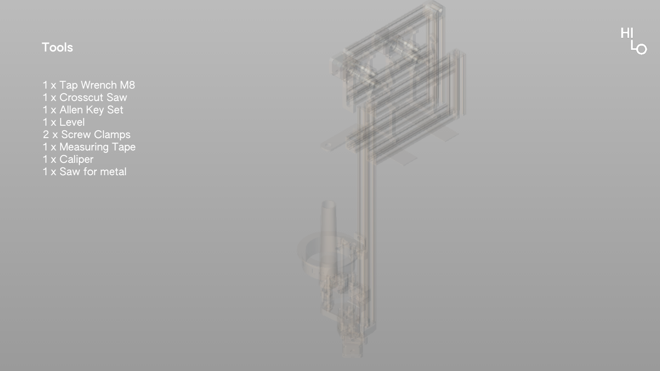
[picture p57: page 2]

1 x Tap Wrench M8
1 x Crosscut Saw
1 x Allen Key Set
1 x Level
2 x Screw Clamps
1 x Measuring Tape
1 x Caliper
1 x Saw for metal

### Tools

### Group: Structure

Components
8 x Profile Typ 3030
15 x Angle slot N8
1 x Hinge for profile 3030 2 x M8x20
30 x M6x10
30 x T-nuts

### Group: Structure

A

B

C

D

Profile Typ 3030
1 x 230 mm

### Group: Structure A

Profile Typ 3030
1 x 113 mm

1 x Angle slot M8

### Group: Structure A

Profile Typ 3030
1 x 230 mm

1 x Angle slot M8

### Group: Structure A

Profile Typ 3030
2x 230 mm | 1 x Angle slot M8

### Group: Structure B

Profile Typ 3030
1 x 230 mm
Group: Structure B | 2 x Angle slot M8

Profile Typ 3030
1 x 230 mm

### Group: Structure B

Tap wrench M8

1 x Hinge for M8
1 x Cylindrical screw M8x20

Tap wrench M8

### Group: Structure B

Tap wrench M8

Profile Typ 3030
1 x 230 mm
1 x Cylindrical screw M8x20

### Group: Structure B

Structure A+B

### Group: Structure C

Profile Typ 3030
2x 230 mm

2 x Angle slot M8

### Group: Structure C

Profile Typ 3030
2x 230 mm
2 x Angle slot M8

### Group: Structure C

Profile Typ 3030
1x 540 mm

3 x Angle slot M8

### Group: Structure D

3x Angle slot M8

Profile Typ 3030
1x 540 mm

### Group: Structure D

Tap wrench M8

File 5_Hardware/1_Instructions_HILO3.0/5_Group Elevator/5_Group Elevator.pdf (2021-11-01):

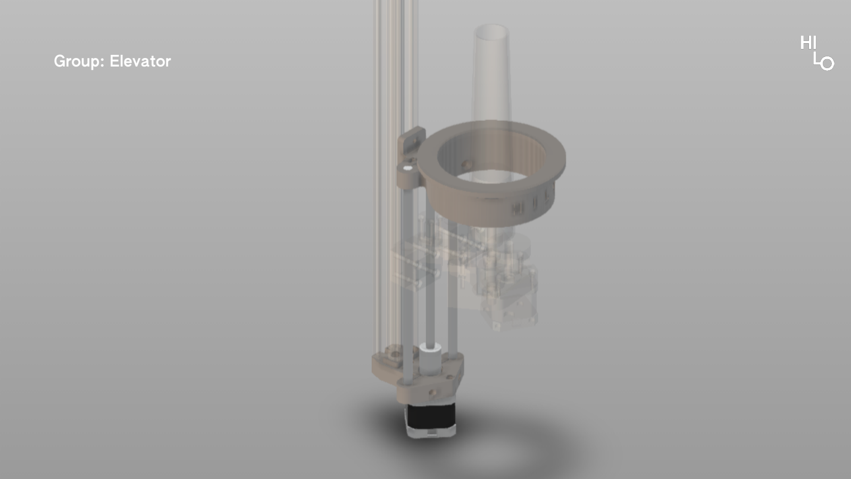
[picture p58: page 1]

### Group: Elevator

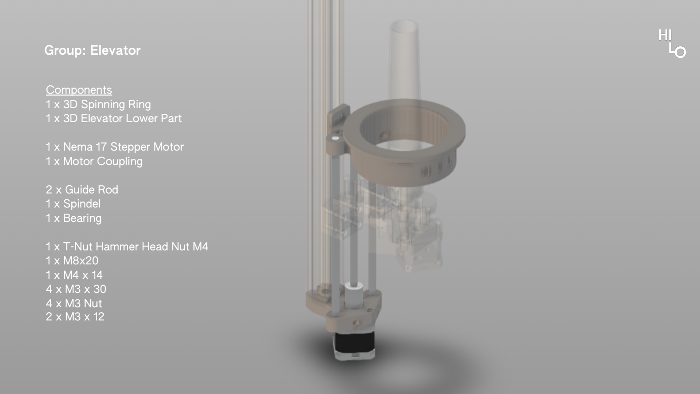
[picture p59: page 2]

### Group: Elevator

Components
1 x 3D Spinning Ring
1 x 3D Elevator Lower Part

1 x Nema 17 Stepper Motor
1 x Motor Coupling

2 x Guide Rod
1 x Spindel
1 x Bearing

1 x T-Nut Hammer Head Nut M4 1 x M8x20
1 x M4 x 14
4 x M3 x 30
4 x M3 Nut
2 x M3 x 12

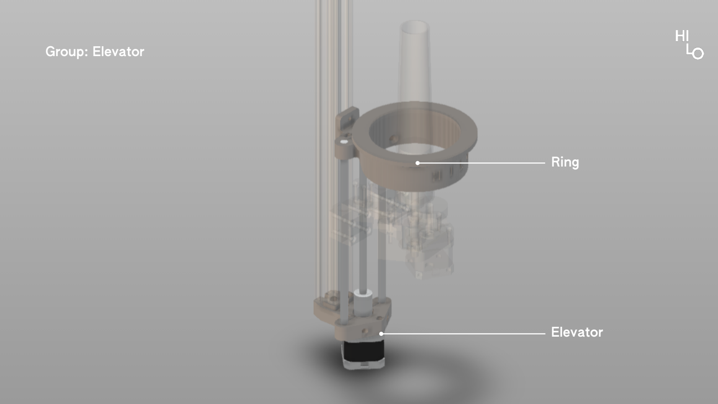
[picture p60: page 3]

### Ring

### Elevator

### Group: Elevator

### Group: Elevator

1 x 3D Elevator Lower Part

### Group: Elevator

1 x 3D Elevator Lower Part 1 x Nema 17 Stepper Motor

2 x M3 x 10

### Group: Elevator

1 x 3D Elevator Lower Part 1 x Nema 17 Stepper Motor

1 x M3 Nut

1 x M3 x 30

### Group: Elevator

2 x Guide Rod

### Group: Elevator

1 x Motor Coupling

### Group: Elevator

1 x Spindel

### Group: Elevator

1 x Spindel Plattform

### Group: Elevator

1 x Spindel Plattform

### Group: Elevator

1 x 3D Spinning Ring

### Group: Elevator

1 x 3D Spinning Ring | 1 x Bearing

### Group: Elevator

1 x 3D Spinning Ring

1 x T-Nut Hammer Head Nut M4 1 x M4 x 14

### Group: Elevator

1 x 3D Spinning Ring

1 x M8x20

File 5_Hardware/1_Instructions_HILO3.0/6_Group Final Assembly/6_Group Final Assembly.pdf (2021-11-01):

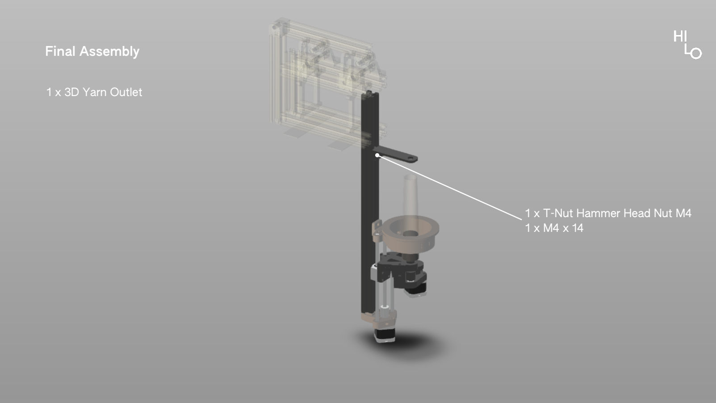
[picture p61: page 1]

1 x T-Nut Hammer Head Nut M4 1 x M4 x 14

### Final Assembly

1 x 3D Yarn Outlet

### Final Assembly

Group: Structure

### Final Assembly

Group: Structure

### Final Assembly

1 x 3D Yarn Guide Back

### Final Assembly

Group: Drive Wheel 1

1 x 3D Yarn Guide front

### Final Assembly

### Final Assembly

Group: Drive Wheel 2

### Final Assembly

Group: Trailing Wheel 1

Group: Trailing Wheel 1

### Final Assembly

Group: Trailing Wheel 1

### Final Assembly

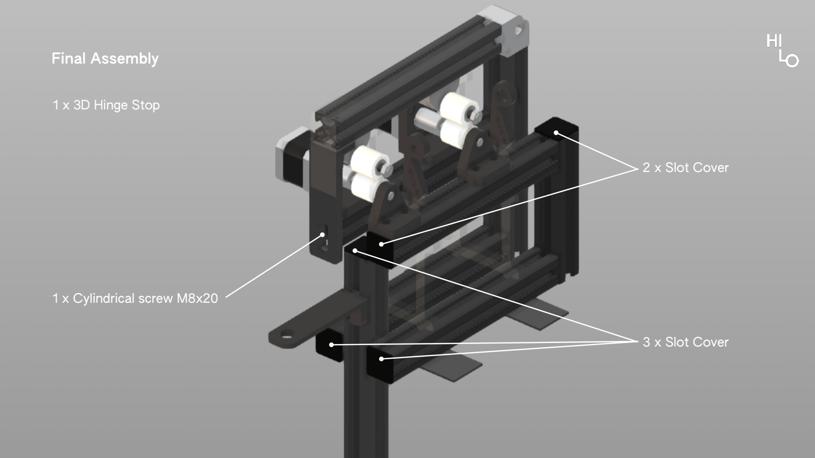
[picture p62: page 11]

1 x 3D Hinge Stop

### Final Assembly

1 x Cylindrical screw M8x20

3 x Slot Cover

2 x Slot Cover

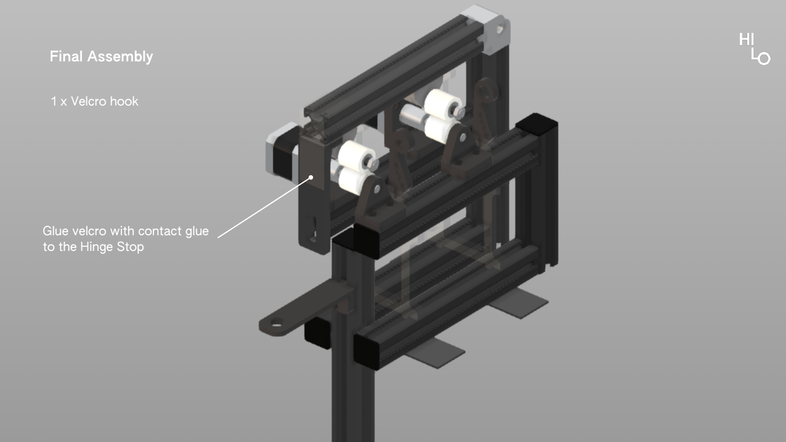
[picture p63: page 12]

1 x Velcro hook

### Final Assembly

Glue velcro with contact glue to the Hinge Stop

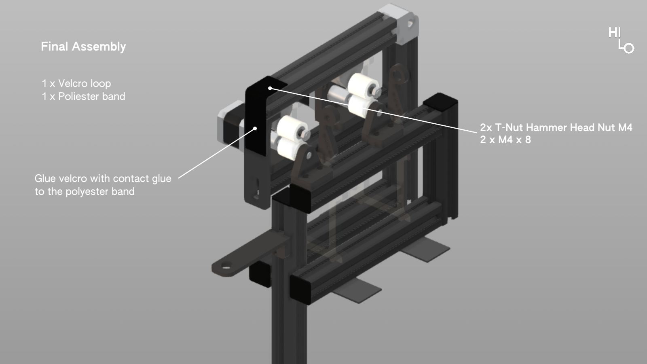
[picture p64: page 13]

1 x Velcro loop
1 x Poliester band

### Final Assembly

2x T-Nut Hammer Head Nut M4 2 x M4 x 8

Glue velcro with contact glue to the polyester band

### Final Assembly

### Final Assembly

1 x 3D Spindel

# HILO SPINNING

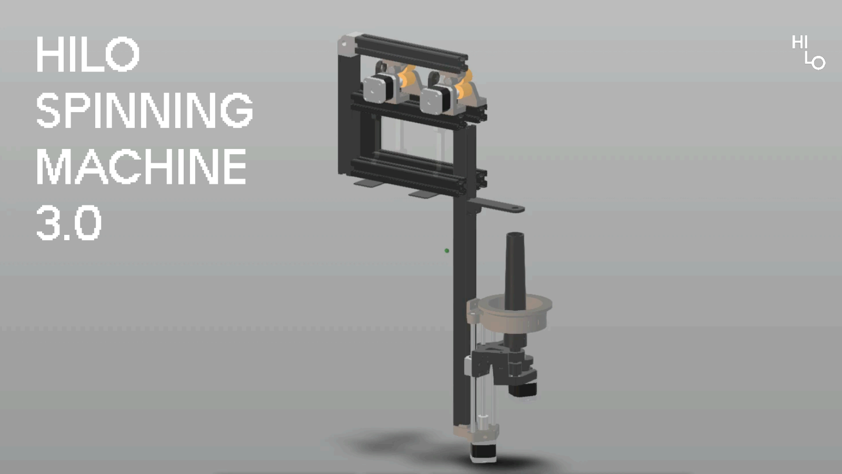
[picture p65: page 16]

# MACHINE

3.0

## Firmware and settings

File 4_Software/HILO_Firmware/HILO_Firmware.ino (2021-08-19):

// Main Tab.
// This tab contains the definitions for the HILO communication protocol
// and the main Arduino functions

#include <AccelStepper.h>

#define HILO_VERSION "HILO Firmware 0.1.0"


// #define USE_START_STOP  // uncomment when using a start/stop button on the machine
// #define HILO_DEBUG         // comment to suppress debug messages

// serial port speed; must be the same in the app
#define HILO_SERIAL_BAUDRATE 115200


// Protocol definitions ==============================================

// Command delimiters
#define CMD_DELIM_BEGIN '['
#define CMD_DELIM_END   ']'
#define CMD_DELIM_PARAM ','

// Commands (settings)
#define CMD_DELIVERY_SPEED 'D'  // [D]elivery
#define CMD_SPINDLE_SPEED  'P'  // s[P]indle
#define CMD_ELEVATOR_SPEED 'L'  // e[L]evator

// Commands (spin)
#define CMD_RUN            'R'  // [R]un
#define CMD_STOP           'S'  // [S]top

// Commands (other)
#define CMD_PING           'A'
#define CMD_INFO           'I'  // [I]nfo
#define CMD_STATUS         'T'  // s[T]atus
#define CMD_ELEVATOR_RESET 'V'  // ele[V]ate  

// Error/Debug
#define CMD_ERROR          'E'
#define CMD_DEBUG          'X'

// Error codes
#define ERR_BUFF_FULL       1   // buffer is full
#define ERR_BEGIN_MISSING   2   // no begin delimiter
#define ERR_END_MISSING     3   // no end delimiter
#define ERR_DATA_SIZE       4   // command is too small (less than 3 bytes)
#define ERR_DELIM           5   // unknow delimiter/character
#define ERR_UNKNOWN_CMD     6   // unknown command
#define ERR_PARAM_COUNT     7   // wrong number of parameters
#define ERR_VALUE_SPEED     8   // speed value invalid or speed value pair inconsistent
#define ERR_BUSY            9   // machine is busy (spinning or resetting)
#define ERR_NO_DEBUG       10   // firmware isn't debug-able


// Buffer for incoming commands (from Serial)
#define COMMAND_BUFF_SIZE 64
char commandBuff [COMMAND_BUFF_SIZE];
int  commandBuffPos = 0;

// Storage for parsed commands
#define MAX_NUM_PARAMS 10
char parsedCommand     = 0;
int  parsedParamsCount = 0;
int  parsedParams [MAX_NUM_PARAMS];


void setup() {
  initMachineControlPins();
  initMachineControlSteppers();

  Serial.begin(HILO_SERIAL_BAUDRATE);
}


void loop() {
  serialCommunicationLoop();
  machineControlLoop();
}


// Reads from the serial port, buffering until a complete message is received.
// Once a complete message has been buffered, parses the contents and handles the requested command.
void serialCommunicationLoop() {
  if (Serial.available() > 0) {
    // read a character from serial, if one is available
    int data = Serial.read();
    
    if (data == 10 || data == 13) {
      // ignore CR and LF
    }
    else {
      // add the character to our buffer until we have a complete message
      commandBuff[commandBuffPos++] = (char)data;
      if (commandBuffPos >= COMMAND_BUFF_SIZE) {
        printError(ERR_BUFF_FULL);
        commandBuffPos = 0;
      }
      else if (data == CMD_DELIM_END) {
        // when the end delimiter is received, parse the buffer contents (a complete message)
        int parseResult = parseData(commandBuff, commandBuffPos);
        commandBuffPos = 0;
        if (parseResult != 0) {
          printError(parseResult);
        }
        else {
          // handle the parsed command and parameters
          handleCommand(parsedCommand, parsedParams, parsedParamsCount);
        }
      }
    }
  }
}


// Handles a command according to the HILO communication protocol,
// by invoking machine control functions. 
void handleCommand(char command, int* params, int numParams) {
  switch (command) {
    case CMD_RUN:
      handleCommandRun();
      break;
    case CMD_STOP:
      handleCommandStop();
      break;
    case CMD_DELIVERY_SPEED:
      handleCommandDeliverySpeed();
      break;
    case CMD_SPINDLE_SPEED:
      handleCommandSpindleSpeed();
      break;
    case CMD_ELEVATOR_SPEED:
      handleCommandElevatorSpeed();
      break;
    case CMD_PING:
      handleCommandPing();
      break;
    case CMD_ELEVATOR_RESET:
      handleCommandElevatorReset();
      break;
    case CMD_INFO:
      handleCommandInfo();
      break;
    case CMD_STATUS:
      handleCommandStatus();
      break;
    default:
      printError(ERR_UNKNOWN_CMD);
      break;
  }
}

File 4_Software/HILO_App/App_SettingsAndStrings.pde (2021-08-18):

// App - Settings and Strings
// Contains classes that load, store and save:
// - App Settings (e.g. screen size, MRU serial port)
// - Machine Settings (machine configuration parameters)
// - App Strings (localized text that is used in the app)

import java.util.Map;
import java.util.Iterator;


// Loads, stores and saves app Settings
class AppSettings {
  
  boolean fullscreen;  // running fullscreen
  int     width;       // window width
  int     height;      // window height
  String  langFile;    // name of the language file to use
  String  prefPort;    // name of the last connected serial port 
  
  AppSettings() {
    resetToDefault();
  }
  
  // Assign default values to the object's fields
  void resetToDefault() {
    this.fullscreen = false;
    this.width      = 1024;
    this.height     = 768;
    this.langFile   = "HILO_AppText_EN.json";
    this.prefPort   = "";
  }
  
  // Load the settings from a file specified by filename (including path)
  boolean load(String filename) {
    JSONObject jsonObj;
    try {
      jsonObj = loadJSONObject(filename);
    } catch (Exception e) {
      return false;
    }
    try {
      this.fullscreen = jsonObj.getBoolean("fullscreen");
      this.width      = jsonObj.getInt    ("width");
      this.height     = jsonObj.getInt    ("height");
      this.langFile   = jsonObj.getString ("langFile");
      this.prefPort   = jsonObj.getString ("prefPort");
    } catch (Exception e) {
      println("AppSettings.load() ERROR: file [" + filename + "] isn't properly formatted");
      println(e.getMessage());
      this.resetToDefault();
      return false;
    }
    if (this.langFile == null) {
      println("AppSettings.load() ERROR: file [" + filename + "] isn't properly formatted (missing String)");
      this.resetToDefault();
      return false;
    }
    return true;
  }
  
  // Save the settings to a file specified by filename (including path)
  boolean save(String filename) {
    JSONObject jsonObj = new JSONObject();
    jsonObj.setBoolean("fullscreen", this.fullscreen);
    jsonObj.setInt    ("width",      this.width);
    jsonObj.setInt    ("height",     this.height);
    jsonObj.setString ("langFile",   this.langFile);
    jsonObj.setString ("prefPort",   this.prefPort);
    try {
      return saveJSONObject(jsonObj, filename);
    } catch (Exception e) {
      println("AppSettings.save() ERROR: can't write to file [" + filename + "]");
      println(e.getMessage());
      return false;
    }
  }
  
  // Overrides the default toString() method, useful for printing the object to the console
  @Override
  String toString() {
    String result = "";
    result += "fullscreen: " + this.fullscreen + "\n";
    result += "width: " + this.width + "\n";
    result += "height: " + this.height + "\n";
    result += "langFile: " + this.langFile;
    result += "prefPort: " + this.prefPort;
    return result;
  }
}
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

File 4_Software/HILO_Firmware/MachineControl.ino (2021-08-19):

// Machine Control.
// This tab contains the definitions for machine pins and hardware
// and functions that drive the machine's behavior.


#define PIN_LED               13  // Arduino on-board LED

#define PIN_START_STOP        19  // RAMPS pin for run/stop switch (last endstop, Z positive)
#define PIN_ELEVATOR_ENDSTOP   3  // RAMPS pin for the first endstop (X negative)

#define PIN_DRAFTING_STEP     54  // Drafting Motor Step Pin
#define PIN_DRAFTING_DIR      55  // Drafting Motor Direction Pin
#define PIN_DRAFTING_ENABLE   38  // Drafting Motor Enable Pin

#define PIN_DELIVERY_STEP     60  // Delivery Motor Step Pin
#define PIN_DELIVERY_DIR      61  // Delivery Motor Direction Pin
#define PIN_DELIVERY_ENABLE   56  // Delivery Motor Enable Pin

#define PIN_SPINDLE_STEP      46  // Spindle Motor Step Pin
#define PIN_SPINDLE_DIR       48  // Spindle Motor Direction Pin
#define PIN_SPINDLE_ENABLE    62  // Spindle Motor Enable Pin

#define PIN_ELEVATOR_A_STEP   26  // Elevator Motors Step Pin
#define PIN_ELEVATOR_A_DIR    28  // Elevator Motors Direction Pin
#define PIN_ELEVATOR_A_ENABLE 24  // Elevator Motors Enable Pin

#define PIN_ELEVATOR_B_STEP   36  // Elevator Motors Step Pin
#define PIN_ELEVATOR_B_DIR    34  // Elevator Motors Direction Pin
#define PIN_ELEVATOR_B_ENABLE 30  // Elevator Motors Enable Pin


#define STEPPER_MAX_SPEED     1000   // speed cap for all stepper motors
#define STEPPER_ACCELERATION  0.01f  // acceleration for all stepper motors (in steps per second per second)

// Speeds in steps (except in old machine's spindle).

// Default drafting and delivery speeds are negative, given the motor orientation in new machine.
#define DEFAULT_DRAFTING_SPEED         -160
#define DEFAULT_DELIVERY_SPEED         -240
#define DEFAULT_SPINDLE_SPEED           700  
#define DEFAULT_ELEVATOR_SPEED          200
#define DEFAULT_ELEVATOR_RESET_SPEED    500
#define ELEVATOR_HEIGHT_STEPS        -18000
#define ELEVATOR_RESET_STEPS          -1000


AccelStepper motorDrafting(AccelStepper::DRIVER, PIN_DRAFTING_STEP, PIN_DRAFTING_DIR);
AccelStepper motorDelivery(AccelStepper::DRIVER, PIN_DELIVERY_STEP, PIN_DELIVERY_DIR);
AccelStepper motorElevatorA(AccelStepper::DRIVER, PIN_ELEVATOR_A_STEP, PIN_ELEVATOR_A_DIR);
AccelStepper motorElevatorB(AccelStepper::DRIVER, PIN_ELEVATOR_B_STEP, PIN_ELEVATOR_B_DIR);
AccelStepper motorSpindle  (AccelStepper::DRIVER, PIN_SPINDLE_STEP,    PIN_SPINDLE_DIR);


// the current speeds for the steppers
int draftingSpeed  = DEFAULT_DRAFTING_SPEED;
int deliverySpeed  = DEFAULT_DELIVERY_SPEED;
int spindleSpeed   = DEFAULT_SPINDLE_SPEED;
int elevatorSpeed      = DEFAULT_ELEVATOR_SPEED;
int elevatorResetSpeed = DEFAULT_ELEVATOR_RESET_SPEED; // current speed for the elevator when resetting its position

// the current drafting speed as a percentage of the delivery speed (integer from 0 to 100)
int draftingSpeedPerc = (DEFAULT_DRAFTING_SPEED * 100) / DEFAULT_DELIVERY_SPEED;

int valueEndstop = LOW;    // current value of the elevator's endstop
int valueStartStop = LOW;  // current value of the start/stop button (when used)

// time at which the start/stop button was last triggered (when used)
unsigned long timeLastStartStop = 0; 

// machine state flags
bool isSpinning          = false;
bool isElevatorResetting = false;

// machine state (i.e., latest command)
char currentState      = CMD_STOP;


// Initializes the pins (input/output) used to control the motor drivers.
void initMachineControlPins() {
  pinMode(PIN_LED, OUTPUT);
  digitalWrite(PIN_LED, LOW);

  // set the mode for the stepper driver enable pins
  pinMode (PIN_DRAFTING_ENABLE,   OUTPUT);
  pinMode (PIN_DELIVERY_ENABLE,   OUTPUT);
  pinMode (PIN_ELEVATOR_A_ENABLE, OUTPUT);
  pinMode (PIN_ELEVATOR_B_ENABLE, OUTPUT);
  pinMode (PIN_SPINDLE_ENABLE,    OUTPUT);
}


// Initializes the stepper motor via the AccelStepper objects
void initMachineControlSteppers() {
  setupStepper(motorDrafting, draftingSpeed);
  setupStepper(motorDelivery, deliverySpeed);
  
  setupStepper(motorElevatorA, elevatorSpeed);
  setupStepper(motorElevatorB, elevatorSpeed);
  setupStepper(motorSpindle, spindleSpeed);

  // disable steppers while not in use
  setSteppersEnabled(false);
}


// Sets up a stepper motor via it's AccelStepper object
void setupStepper(AccelStepper & stepper, int motorSpeed) {
  stepper.setMaxSpeed(STEPPER_MAX_SPEED);
  stepper.setAcceleration(STEPPER_ACCELERATION);
  stepper.setSpeed(motorSpeed);
}


// Enables or disables all steppers. Used for saving power
// and allowing adjustments by hand when the machine isn't running.
void setSteppersEnabled(bool enabled) {
  int value = LOW;
  if (!enabled) value = HIGH;

  digitalWrite(PIN_DRAFTING_ENABLE,   value);
  digitalWrite(PIN_DELIVERY_ENABLE,   value);
  digitalWrite(PIN_ELEVATOR_A_ENABLE, value);
  digitalWrite(PIN_ELEVATOR_B_ENABLE, value);
  digitalWrite(PIN_SPINDLE_ENABLE,    value);
}


// Enables or disables elevator steppers
void setElevatorSteppersEnabled(bool enabled) {
  int value = LOW;
  if (!enabled) value = HIGH;
  
  digitalWrite(PIN_ELEVATOR_A_ENABLE, value);
  digitalWrite(PIN_ELEVATOR_B_ENABLE, value);
}


// Handles a "ping" command by sending back a "ping"
void handleCommandPing() {
  printReply(CMD_PING);
}


// Resets the elevator's position (unless the machine is spinning or already resetting the elevator)
void handleCommandElevatorReset() {
  if (isSpinning) {
    printMessage("handleCommandElevatorReset() ERROR: machine is currently spinning");
    printError(ERR_BUSY);
  }
  else if (isElevatorResetting) {
    printMessage("handleCommandElevatorReset(): elevator is already resetting");
    printReply(CMD_ELEVATOR_RESET);
  }
  else {
    printMessage("handleCommandElevatorReset(): resetting elevator");
    isElevatorResetting = true;
    setElevatorSteppersEnabled(true);
    currentState = CMD_ELEVATOR_RESET;
    motorElevatorA.setCurrentPosition(0);
    motorElevatorB.setCurrentPosition(0);
    motorElevatorA.setSpeed(elevatorResetSpeed);
    motorElevatorB.setSpeed(elevatorResetSpeed);
    digitalWrite(PIN_LED, HIGH);
    printReply(CMD_ELEVATOR_RESET);
  }
}
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

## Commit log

2021-07-14 Inicial commit
    [190129_Spindel Halter.3dm, HILO_MachineSettings.json, Huelse.IGS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]
2021-08-18 Upload New File
    [HILO3.0_List_of_Parts.xlsx]
2021-09-09 Uploaded newly formated BOM.md
2021-09-09 Renamed BOM.md to List-of-Parts
2021-10-16 Update 9_HILO_App/HILO_App/data/fonts/.gitkeep, 9_HILO_App/HILO_App/data/fonts/Objectivity-Bold.otf, 9_HILO_App/HILO_App/data/fonts/Objectivity-Regular.otf, 9_HILO_App/HILO_App/data/icons/large/.gitk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
    [HILO_MachineSettings.json]
2021-10-16 Update 6_HILO_App/HILO_App/data/fonts/.gitkeep, 6_HILO_App/HILO_App/data/fonts/Objectivity-Bold.otf, 6_HILO_App/HILO_App/data/fonts/Objectivity-Regular.otf, 6_HILO_App/HILO_App/data/icons/large/.gitk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
    [HILO_MachineSettings.json]
2021-10-26 Update 4_Build_HILO Spinning Machine/3_Connect_HILO App, Processing and Arduino/Step_by_Step_Connect_HILO Hardware &amp; App.docx Deleted 5_Connect_HILO Hardware &amp; App/Step_by_Step_Connect_HILO_H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
2021-10-26 Update 2_List of Parts/HILO3.0_List_of_Parts.pdf, 2_List of Parts/HILO3.0_List_of_Parts.xlsx, 2_List of Parts/List-of-Parts.md, 2_List of Parts/readme_order_material_list.pdf, 3_Files/1_Readme_ 3-D p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
    [Axle_holder_trailing_wheel.stl, Axle_holder_trailing_wheel_2.stl, Elevator_lower_part.stl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]
2021-10-26 Update 3_Files/2_3D CAD/3D CAD Parts/Filament/Readme_How to Print with Filament.docx
2021-10-26 Update 3_Files/2_3D CAD/3D CAD Parts/PolyJet/Drive wheel/Drive_wheel_Soft.stl, 3_Files/2_3D CAD/3D CAD Parts/PolyJet/Drive wheel/Drive_wheel_Hard.stl files
    [Drive_wheel_Hard.stl, Drive_wheel_Soft.stl]
2021-10-26 Deleted 3_Files/2_3D CAD/3D CAD Parts/Filament/Readme_How to Print with Filament.docx
2021-10-26 Update 3_Files/2_3D CAD/3D CAD Parts/PolyJet/Trailing wheel/Trailing_wheel_Soft.stl, 3_Files/2_3D CAD/3D CAD Parts/PolyJet/Trailing wheel/Trailing_wheel_Hard.stl, 3_Files/2_3D CAD/3D CAD Parts/PolyJe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
    [Trailing_wheel_Hard.stl, Trailing_wheel_Soft.stl]
2021-10-26 Update 3_Files/2_3D CAD/HILO Spinning Machine/Fusion/210629_HILO_Top_Assembly v14.f3d
    [210629_HILO_Top_Assembly v14.f3d]
2021-10-26 Update 5_HILO_App/HILO_App/data/fonts/.gitkeep, 5_HILO_App/HILO_App/data/fonts/Objectivity-Bold.otf, 5_HILO_App/HILO_App/data/fonts/Objectivity-Regular.otf, 5_HILO_App/HILO_App/data/icons/large/.gitk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
    [HILO_MachineSettings.json]
2021-11-01 Update 2_List of Parts/List of Parts.xlsx Deleted 2_List of Parts/HILO3.0_List_of_Parts.pdf, 2_List of Parts/HILO3.0_List_of_Parts.xlsx, 2_List of Parts/readme_order_material_list.pdf files
    [HILO3.0_List_of_Parts.xlsx, List of Parts.xlsx]
2021-11-01 Update 4_Build_HILO Spinning Machine/Connect_HILO App, Processing and Arduino/media/image1.jpg, 4_Build_HILO Spinning Machine/Connect_HILO App, Processing and Arduino/media/image10.png, 4_Build_HILO 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
    [1_Group Structure.xlsx, 2_Group Drive Wheel .xlsx, 3_Group Trailing Wheel.xlsx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]
2021-11-01 Deleted 4_Build_HILO Spinning Machine/Connect_HILO App, Processing and Arduino/media/image1.jpg, 4_Build_HILO Spinning Machine/Connect_HILO App, Processing and Arduino/media/image10.png, 4_Build_HILO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
2021-11-01 Update 4_Build_HILO Spinning Machine/3_Connect_HILO App, Processing and Arduino/How to Start_Software &amp; Hardware.pdf, 4_Build_HILO Spinning Machine/3_Connect_HILO App, Processing and Arduino/Step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
2021-11-01 Update 4_Build_HILO Spinning Machine/Connect_HILO App, Processing and Arduino/How to Start_Software &amp; Hardware.pdf Deleted 4_Build_HILO Spinning Machine/3_Connect_HILO App, Processing and Arduino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
2021-11-02 Deleted 2_List of Parts/List of Parts.xlsx
    [List of Parts.xlsx]
2021-11-02 Update 2_List of Parts/List of Parts.xlsx
    [List of Parts.xlsx]
2021-11-02 Update 3_Files/1_Readme_ 3-D printing and laser cutting.docx, 3_Files/3_Laser Cut/Traveler_Acrylic glass_6mm.eps, 2_List of Parts/1_Readme_order_material_list.md, 2_List of Parts/2_List-of-Parts.md, 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
    [1_Group Structure.xlsx, 2_Group Drive Wheel .xlsx, 3_Group Trailing Wheel.xlsx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]
2021-11-02 Update 4_Build_HILO Spinning Machine/3_Connect_HILO App, Processing and Arduino/Step_by_Step_Connect_HILO_Hardware_App.md
2021-11-02 Update 4_Build_HILO Spinning Machine/3_Connect_HILO App, Processing and Arduino/Step_by_Step_Connect_HILO_Hardware_App.md Deleted 5_HILO_App/readme_HILO App.docx
2021-11-02 Update 5_Hardware/1_Instructions_HILO3.0/1_Group Structure/1_Group Structure.pdf, 5_Hardware/1_Instructions_HILO3.0/1_Group Structure/1_Group Structure.xlsx, 5_Hardware/1_Instructions_HILO3.0/2_Group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
    [1_Group Structure.xlsx, 2_Group Drive Wheel .xlsx, 3_Group Trailing Wheel.xlsx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]
2021-11-06 Added Readme for 3D printing and laser cutting in Files folder
2021-11-06 Added Part List Group Drive Wheel in Markdown
